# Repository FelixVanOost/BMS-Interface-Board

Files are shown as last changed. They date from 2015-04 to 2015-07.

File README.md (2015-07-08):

Copyright Felix van Oost 2015.
This documentation describes Open Hardware and is licensed under the CERN OHL v1.2. You may redistribute and modify this documentation under the terms of the [CERN OHL v1.2](http://ohwr.org/cernohl). This documentation is distributed WITHOUT ANY EXPRESS OR IMPLIED WARRANTY, INCLUDING OF MERCHANTABILITY, SATISFACTORY QUALITY AND FITNESS FOR A PARTICULAR PURPOSE. Please see the CERN OHL v1.2 for applicable conditions.

# BMS Interface Board
A PCB to interface some of the main I/O functions of the [Orion BMS](http://www.orionbms.com/) with an electric car.

This project is developed by the [Electric Car Club](http://ubcelectriccar.com/) at the University of British Columbia, whose current goal is to break the world record for the fastest 1/4 mile in a street-legal electric car. The car, named Elektra, is based on a 1963 Volkswagen Beetle.

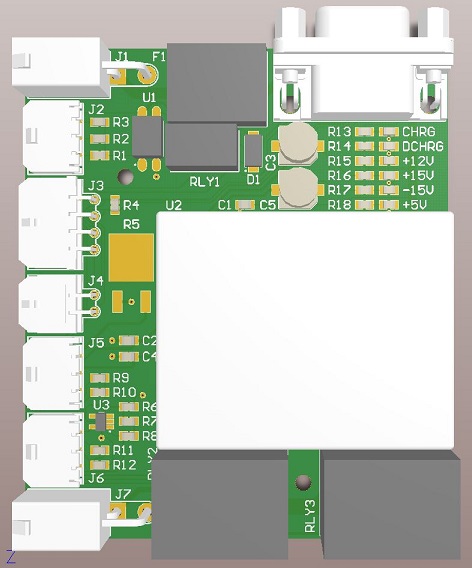
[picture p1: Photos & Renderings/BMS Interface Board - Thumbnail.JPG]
Image of BMS Interface Board

*BMS Interface Board - Rev. A*

----------
Context
----------

In Elekta, the Orion BMS manages a battery pack consisting of 30 [Turnigy 22.2V 6S 5Ah](http://www.hobbyking.com/hobbyking/store/__38515__Turnigy_Heavy_Duty_Series_5000mAh_6S_60C_Lipo_Pack.html) lithium-ion polymer batteries (originally designed for use in R/C airplanes) arranged in 5 series modules of 6 parallel batteries each. This results in a total nominal pack voltage of 111V with a peak discharge current of around 2,400A.

The BMS monitors a variety of parameters, including total pack discharge, pack voltage, cell impedance, and state of charge. It is also responsible for monitoring the charging process of the pack, and is capable of balancing the individual cells within each battery. The addition of a [Thermistor Expansion Module](http://www.orionbms.com/products/thermistor-expansion-module/) allows the BMS to monitor temperature data for each battery, which is a useful safety feature to detect abnormal battery behavior and take action to mitigate possible catastrophic failure before it occurs. The Orion BMS and Thermistor Expansion Module are both powered from a nominal +12V. The BMS actually has two separate power inputs, which are used to place the unit in either charge or discharge mode.

In order to determine state of charge and peak charge / discharge current, the BMS uses a hall-effect current transducer mounted to the positive terminal of the entire battery pack. The transducer we use is a Premo HCT-2000LF, which is capable of measuring peak currents of +/-4,000A with 0.2% accuracy. The transducer requires a +/-15V bipolar power supply capable of delivering 1A continuously.

As a crucial safety measure, the BMS must be able to shut off power to both the battery pack and the charger to protect the batteries from damage. The Charge and Discharge Enable outputs on the BMS toggle on when the BMS determines that the battery pack is either ready to be charged or discharged. In Elektra, these outputs are connected to the main battery pack contactor circuit, which isolates the pack from the rest of the car. As such, the BMS has the ability to completely shut off power going into and out of the battery pack if it detects abornamal behaviour (e.g. the maximum discharge current limit has been exceeded or one of the batteries is getting too hot). The Charge Safety output is used as a backup safety measure to shut off charging current from entering the battery pack. Under normal circumstances, the Orion BMS communicates with the charger over CAN, controlling and monitoring the charging process. In this setup, the charger only has to provide the power that the BMS requests (the BMS has full control over the charging process). In a scenario where the BMS requests the charger to terminate charging and a malfunction or communication error occurs, however, the unit can toggle off the Charge Safety output to completely isolate the battery pack from the charger. In Elektra, this output is connected to a seperate charging contactor, which isolates the pack from the charging port on the side of the car.

----------
Functionality
----------

The BMS Interface Board acts as a central physical hub to help integrate the Orion battery management system with existing circuits inside the car. It incorporates the following functionality:

- Provides fused power distribution to the BMS (+12V), the Thermistor Expansion Module (+12V), and the hall-effect current transducer (+/-15V) both whilst driving and charging.
- Interfaces the open drain Charge Safety, Discharge Enable, and Charge Enable outputs from the BMS with their corresponding circuits in the car via relays.
- Converts the current output of the Premo current transducer to a 1-4V input signal for the BMS.
- Connects the Thermistor Expansion Module to the BMS via the CAN1 bus and outputs CAN1 to a DB9 connector to interface with the Orion CANdapter (a CAN-to-USB adapter used for BMS programming purposes and firmware updates).

----------
Specifications
----------

The BMS Interface Board incorporates a blend of both surface-mount and through-hole components based on their size and strength requirements. Surface-mount parts are 2012-sized where possible to simplify the PCB assembly process.

- An automotive-style 3A MINI blade fuse on the main +12V power rail protects the 12V circuitry in the car.

- To toggle the BMS between charge and discharge modes, an SPDT relay switches power to the appropriate power pin via a photocoupler and a set of current-limiting resistors. A flyback diode is incorporated into the design to prevent damage to the photocoupler as the relay is switched off. The BMS enters charge mode when the relay is switched off and discharge mode when the relay is switched on. The Interface Board accommodates 3.3V, 5V, or 12V inputs to switch the relay, which enables the BMS state to be set either by a microcontroller or a manual toggle switch connected to Elektras' 12V circuit.

- A pair of relays are used to interface the Charge Safety output to the charging contactor and the Discharge / Charge Enable outputs to the main contactors. The relays have been sized to accommodate a maximum switching current of 10A.

- A ±15V, 1A switching DC-DC converter from CUI provides power to the current transducer. A 10uF ceramic capacitor filters the input power to the unit, and a combination of 1uF ceramic and 100uF electrolytic capacitors provide filtering for the two outputs. The converter’s high efficiency (~90%) reduces the need to make special accommodations for heat dissipation on the board (total heat dissipated will peak at around 3W).

- The current transducer has a maximum current measurement capability of ±4,000A, and provides an output signal of ±800mA proportional to its input. The Orion BMS requires a 1-4V input signal (centred at 2.5V), where the range from 1-2.5V is ‘negative’ (charge) current and the remaining 2.5-4V is ‘positive’ (discharge) current. The BMS tolerates readings from 0.5-4.5V to extend the measurement range, but readings outside these bounds will trigger an internal fault. A 2.5Ω burden power resistor produces a ±2V output signal from the ±800mA current transducer output, following which a non-inverting amplifier with a gain of 0.75 converts the input to a ±1.5V signal and offsets the result by 2.5V to produce a 1-4V signal for the Orion BMS. The op-amp has been chosen for its low input offset voltage and fast slew rate to ensure accurate and fast current sensor readings with minimal error.

-	A set of six green LEDs are connected to each of the main supply rails (+12V, +15V, -15V, and +5V) as well as the Charge and Discharge Power outputs to provide visual user feedback for circuit troubleshooting purposes.

-	Molex Micro-Fit connectors are used for signal-level and low-power wiring, which offer a sturdy locking design in a compact package. The main power connector and current sensor connector are Molex Mega-Fit due to the higher currents and larger wire gauge requirement for those connections. All connectors are through-hole mount to ensure physical robustness.

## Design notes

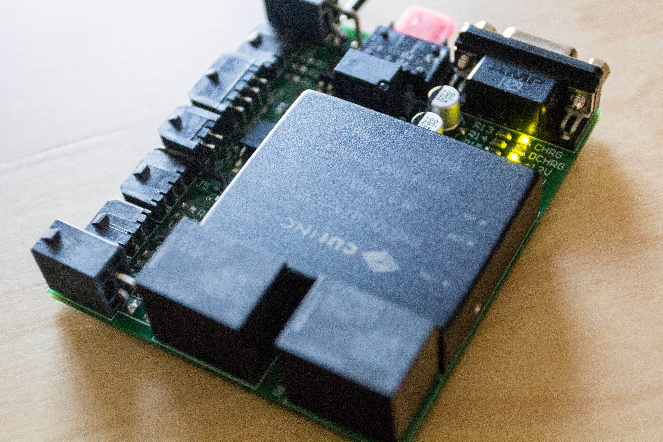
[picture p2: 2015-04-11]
Photos & Renderings/BMS Interface Board 3.jpg

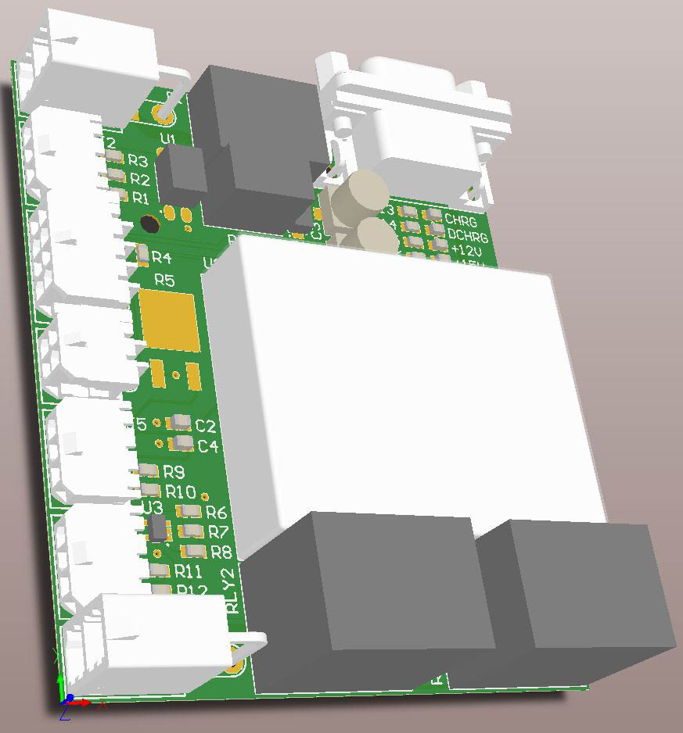
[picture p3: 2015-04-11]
Photos & Renderings/BMS Interface Board 2.JPG

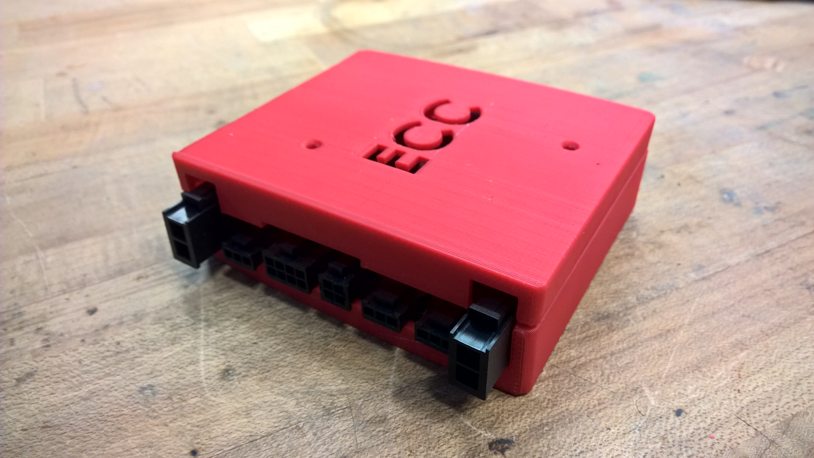
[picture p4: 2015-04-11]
Photos & Renderings/Enclosure 3.jpg

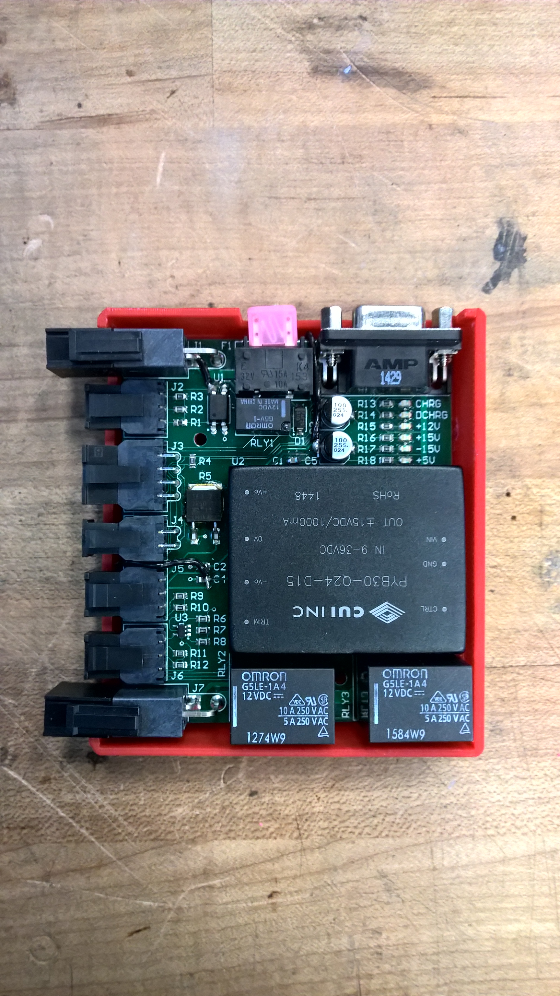
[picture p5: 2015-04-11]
Photos & Renderings/Enclosure 2.jpg

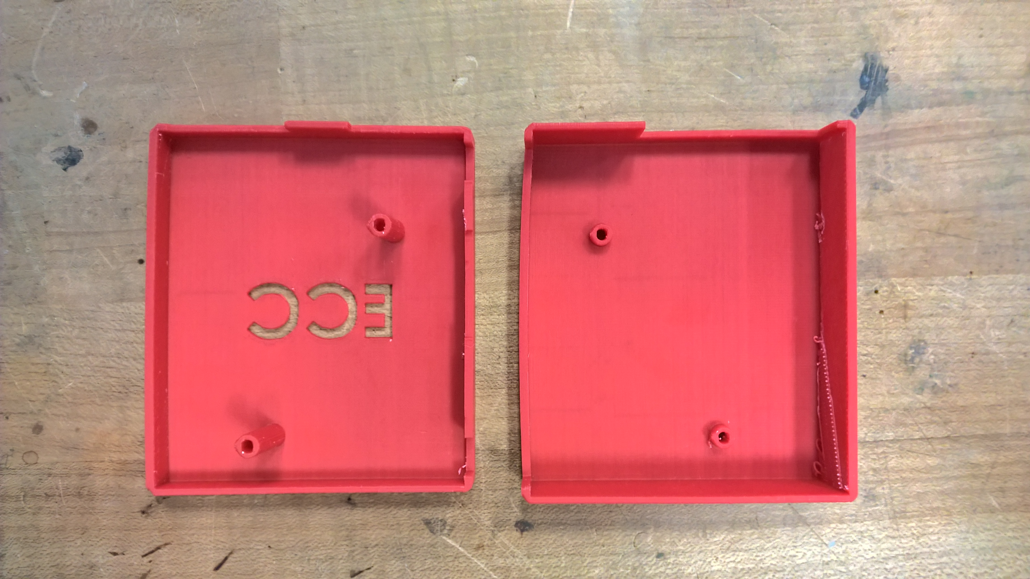
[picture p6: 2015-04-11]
Photos & Renderings/Enclosure 1.jpg

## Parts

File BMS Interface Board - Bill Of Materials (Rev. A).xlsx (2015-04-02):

Part | Package | Digi-Key Part # | Qty. | Price (Each) | Price (Tot.) | Designator
TE Connectivity Right Angle Female DB9 Connector | - | A35107-ND | 1 | $2.12 | $2.12 | J8
Molex Mega-Fit 172064-Series 2-Pin Male Header | - | WM10391-ND | 2 | $3.40 | $6.80 | J1, J7
Molex Micro-Fit 43650-Series 3-Pin Male Header | - | WM1861-ND | 3 | $1.41 | $4.23 | J2, J4, J5, J6
Molex Micro-Fit 43045-Series 4-Pin Male Header | - | WM1814-ND | 1 | $1.83 | $1.83 | J4
Molex Micro-Fit 43045-Series 8-Pin Male Header | - | WM1816-ND | 1 | $2.83 | $2.83 | J3
Littelfuse 153-Series MINI Horizontal Fuse Holder | - | F064-ND | 1 | $4.67 | $4.67 | F1
Littelfuse 4A 32V MINI Fuse |  | F6074-ND | 1 | $0.73 | $0.73 | F1
Molex Mega-Fit 171692-Series 2-Pin Female Connector | - | WM10385-ND | 2 | $1.00 | $2.00 | -
Molex Micro-Fit 43645-Series 3-Pin Female Connector | - | WM1846-ND | 3 | $0.54 | $1.62 | -
Molex Micro-Fit 43025-Series 4-Pin Female Connector | - | WM1784-ND | 1 | $0.61 | $0.61 | -
Molex Micro-Fit 43025-Series 8-Pin Female Connector | - | WM1786-ND | 1 | $0.76 | $0.76 | -
Molex Mega-Fit 12AWG Gold Crimp Contact | - | WM10404CT-ND | 5 | $1.08 | $5.40 | -
Molex Micro-Fit 43030-Series 20-24AWG Tin Crimp Contact | - | WM1837CT-ND | 25 | $0.14 | $3.42 | -
CUI PYB30 Series ±15V 30W DC-DC Converter | 7-DIP | 102-2941-ND | 1 | $62.06 | $62.06 | U2
Omron G5LE-1A4-DC12 5A SPST-NO Relay |  | Z2352-ND | 2 | $1.81 | $3.62 | RLY2, RLY3
Omron G5V-1 DC12 1A SPDT Relay |  | Z774-ND | 1 | $2.77 | $2.77 | RLY1
Lite-On LTV-817S Photocoupler | 4-SMD | 160-1367-5-ND | 1 | $0.55 | $0.55 | U1
Microchip MCP6071T-E/OT Low-Offset Op-Amp | SOT-23-5 | MCP6071T-E/OTCT-ND | 1 | $0.96 | $0.96 | U3
 |  |  |  |  | $0.00
Kemet X7R 1uF 10% 25V Ceramic Capacitor | 2012 | 399-8004-1-ND | 2 | $0.26 | $0.52 | C2, C4
Kemet X5R 10uF 20% 16V Ceramic Capacitor | 2012 | 399-8013-1-ND | 1 | $0.39 | $0.39 | C1
Panasonic EEE-Series 100uF 20% 25V Aluminium Capacitor |  | PCE4595CT-ND | 2 | $0.99 | $1.98 | C3, C5
Panasonic ERJ-Series 100Ω 1% Resistor | 2012 | P100CCT-ND | 1 | $0.14 | $0.14 | R1
Panasonic ERJ-Series 120Ω 1% Resistor | 2012 | P120CCT-ND | 1 | $0.14 | $0.14 | R4
Panasonic ERJ-Series 200Ω 1% Resistor | 2012 | P200CCT-ND | 1 | $0.14 | $0.14 | R2
Panasonic ERJ-Series 300Ω 1% Resistor | 2012 | P300CCT-ND | 1 | $0.14 | $0.14 | R18
Panasonic ERJ-Series 499Ω 1% Resistor | 2012 | P499CCT-ND | 1 | $0.14 | $0.14 | R8
Panasonic ERJ-Series 510Ω 5% 0.5W Resistor | 2012 | P510ADCT-ND | 1 | $0.33 | $0.33 | R3
Panasonic ERJ-Series 1kΩ 1% Resistor | 2012 | P1.00KCCT-ND | 3 | $0.14 | $0.42 | R13, R14, R15
Panasonic ERJ-Series 1.3kΩ 1% Resistor | 2012 | P1.30KCCT-ND | 2 | $0.14 | $0.28 | R16, R17
Panasonic ERJ-Series 2kΩ 1% Resistor | 2012 | P2.00KCCT-ND | 1 | $0.14 | $0.14 | R7
Panasonic ERJ-Series 10kΩ 1% Resistor | 2012 | P10.0KCCT-ND | 2 | $0.14 | $0.28 | R6, R9
Panasonic ERA-Series 10kΩ 0.1% Resistor | 2012 | P10KDACT-ND | 2 | $0.91 | $1.82 | R11, R12
Panasonic ERJ-Series 15kΩ 1% Resistor | 2012 | P15.0KCCT-ND | 1 | $0.14 | $0.14 | R10
Bourns PWR163S-25-Series 25W 1% Power Resistor | TO-252-3 | PWR163S-25-2R50F-ND | 1 | $3.99 | $3.99 | R5
Fairchild S1G Rectifying Diode | DO-214AC | S1GFSCT-ND | 1 | $0.32 | $0.32 | D1
Lite-On LTST-C170GKT Green LED | 2012 | 160-1179-1-ND | 6 | $0.44 | $2.64 | D2-D7
 |  |  |  |  | $120.93

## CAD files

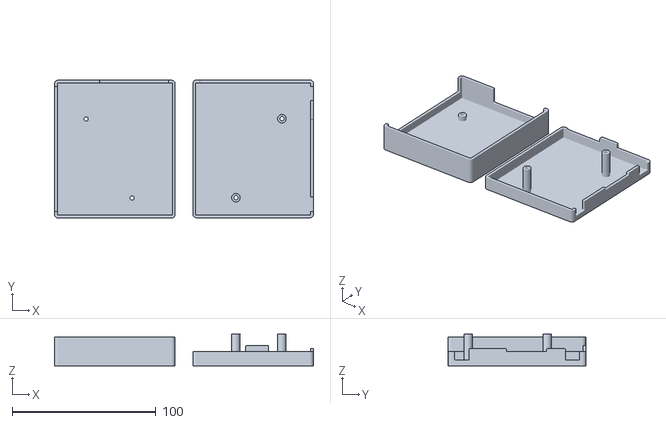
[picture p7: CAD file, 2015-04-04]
Enclosure/BMS Interface Board Enclosure.stl
180.3 x 96.2 x 22.0

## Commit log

2015-04-02 Added Rev. A Gerber Files
    Includes complete files for printing the board and cutting a solder
    paste stencil.
2015-04-02 Added Rev. A Altium Designer Files
    Includes PCB layout and circuit schematic files, PCB and schematic
    component libraries, and CAM output files.
    [BMS Interface Board.PcbDoc, BMS Interface Board.PcbLib, BMS Interface Board.PrjPcb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]
2015-04-02 Added Rev. A Bill Of Materials
    [BMS Interface Board - Bill Of Materials (Rev. A).xlsx]
2015-04-03 Update README.md
    Added 'Functionality' and 'Context' sections to provide an overview of the purpose behind the BMS Interface Board.
2015-04-03 Update README.md
    Added links to the Orion BMS and UBC ECC websites
2015-04-04 Update README.md
    Added board specifications
2015-04-04 Added 3D-printed enclosure files
    Includes an Autodesk 123D file and an exported .stl file
    [BMS Interface Board Enclosure.stl]
2015-04-04 Added CERN OHL v1.2 license information
    [BMS Interface Board.SchDoc]
2015-04-11 Added photo and 3D renderings of board
2015-04-11 Update README.md
    Added 3D rendering of board
2015-04-11 Added photos of 3D-printed enclosure
